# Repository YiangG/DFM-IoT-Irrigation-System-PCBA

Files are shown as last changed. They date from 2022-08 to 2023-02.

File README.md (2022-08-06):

# DFM-IoT-Irrigation-System-PCBA

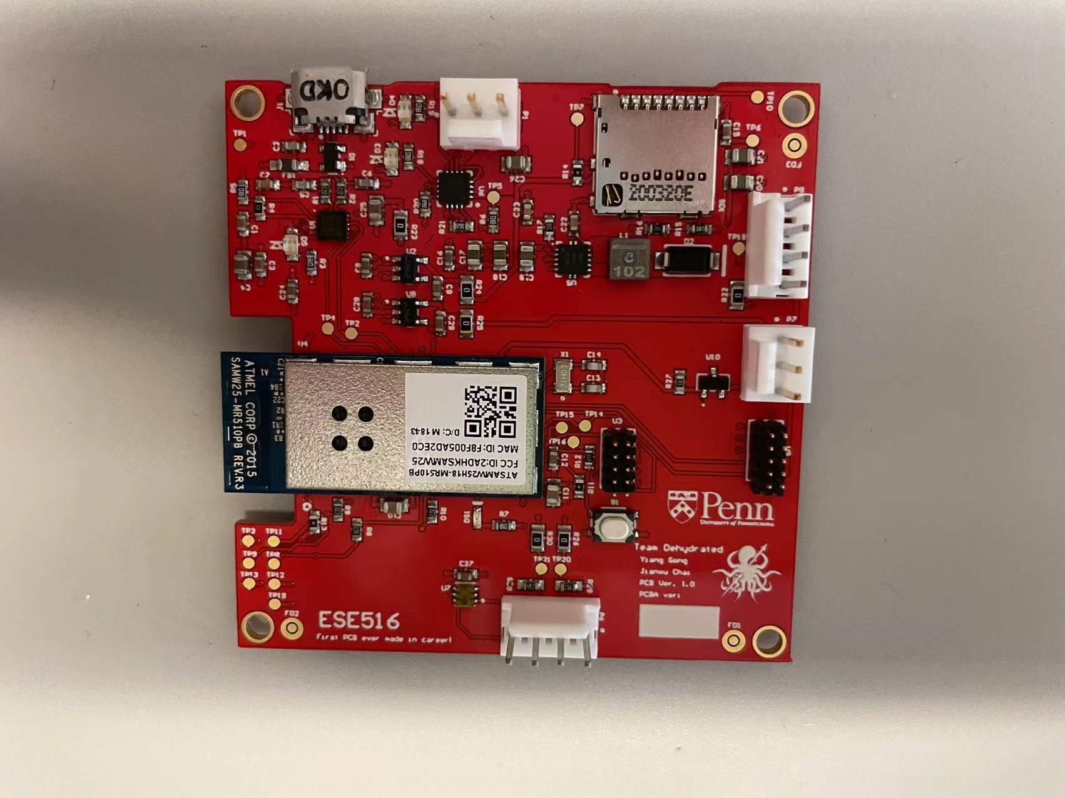
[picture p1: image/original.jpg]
original


This is the output file from Altium Designer from ESE516 class
## What it does
We decided to make a smart irrigation system which could measure the moisture level of soil and irrigate it when it is too dry.

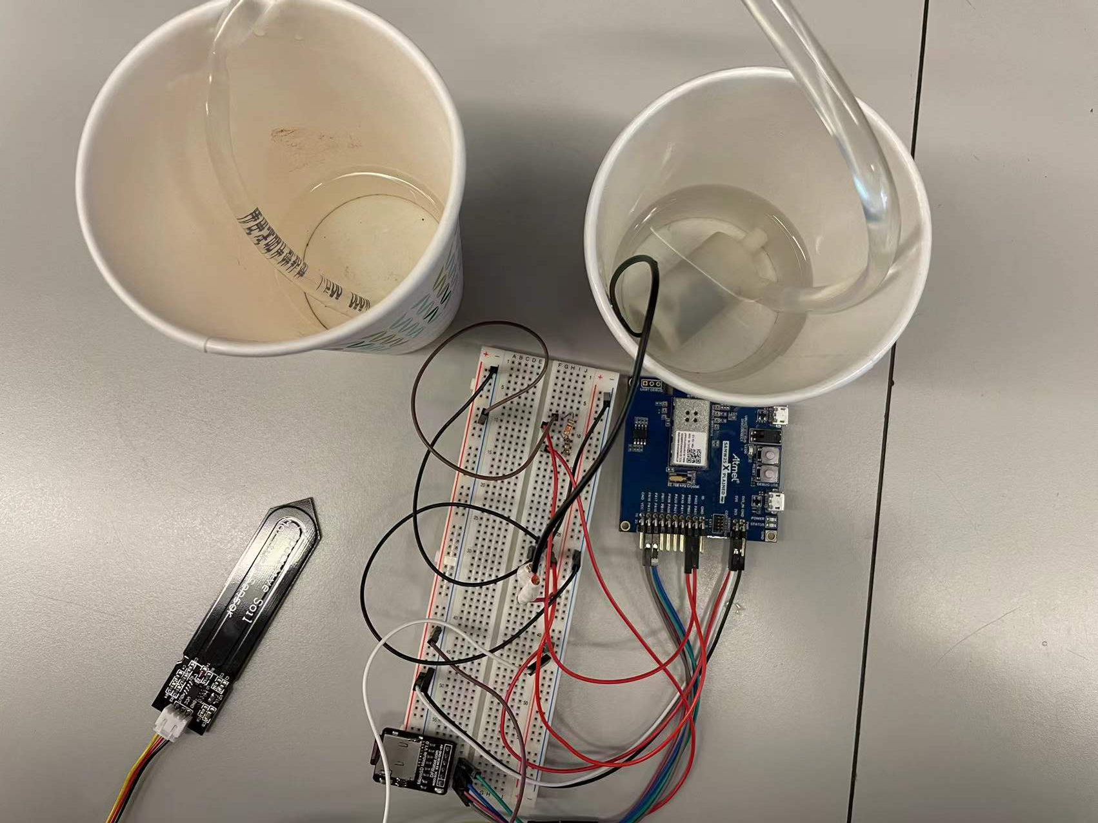
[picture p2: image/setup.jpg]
setup

https://www.youtube.com/watch?v=NsQ1t5cRwfQ

## Inspiration
This device is designed for people who love gardening but travel a lot. Once the device is installed, while the user is away from home, it could alert the user when the soil moisture level drops below a certain threshold, and the user could remotely control the device to water the plants, or to let the device decide when to irrigate the plants.

## How we built it
In this project, we followed the top-down design scheme. So, in the first place, we designed the overall functionalities of the system as shown in the system block diagram. The system is based on the SAMW25 MCU, and it communicate with the soil moisture sensor and the ambient light sensor via I2C and drive the pump and LED array with GPIO. Also, the MCU has the WINC1500 WIFI module so we used this feature to build an IoT product.

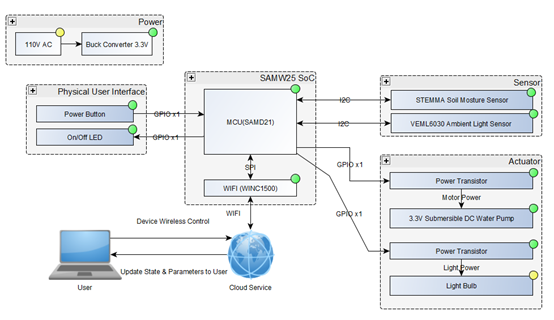
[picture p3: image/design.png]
design


Then we captured the schematics, and started PCBA layout in Altium Designer. The schematic and PCB layout are on the image files above. In the schematics, we used the hierarchical subsheet structure to simplify the main schematic and make it easy to read.

Then we selected proper components and layout them onto the PCBA file. We implemented our design in a 4 layers PCB. It’s quite an interesting experience of designing the PCB, and after that we send this PCB design to PCBWAY, a manufacture in Shenzhen China, to print it out.

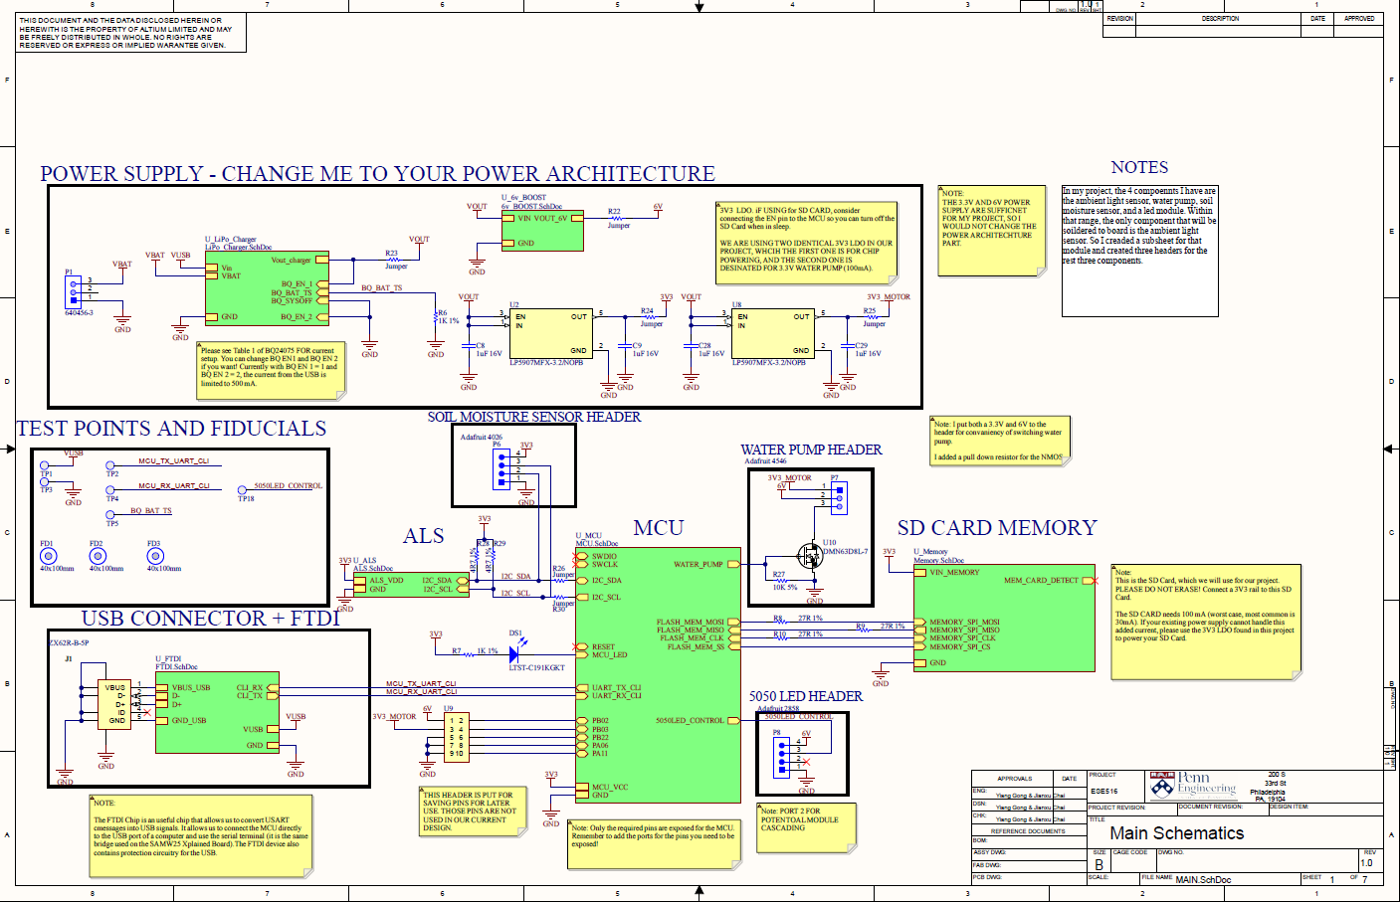
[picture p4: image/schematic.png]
schematic


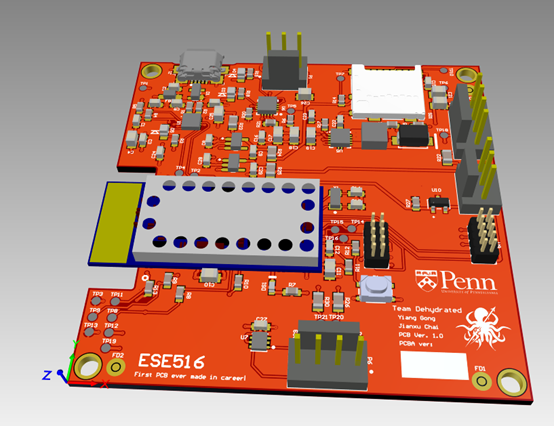
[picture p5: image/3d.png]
3d


After the hardware design, we started on the software side, which we implemented a bootloader, and utilized the FreeRTOS system on our project. Also, our board has command line interface, which we can type some instructions to the terminal and readout the sensor values (soil moisture sensor, IMU, ultrasonic sensor, etc.). Since it’s an IoT project, we implemented web interface (via NodeRed and IBM cloud) as well. The upstream data are being transmitted to the MQTT broker server first and then to the NodeRed interface, which is powered by IBM cloud. We can read sensor value and history in the web interface, as shown in picture above.

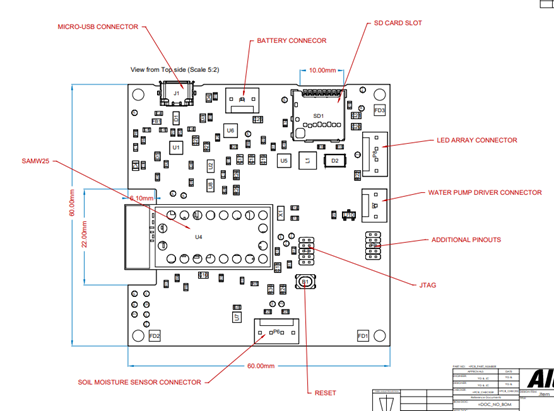
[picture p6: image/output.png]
output


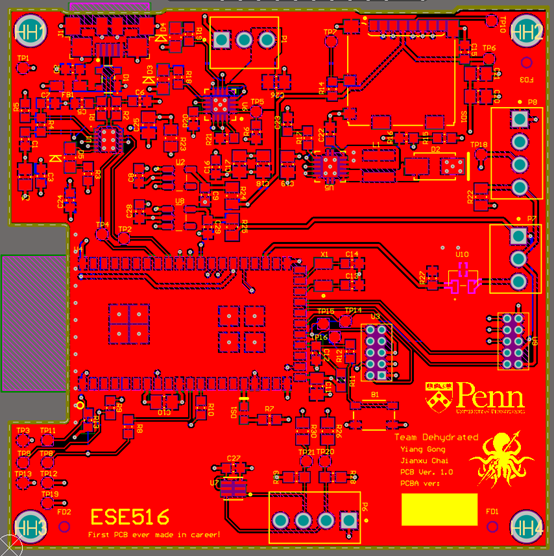
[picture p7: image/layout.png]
layout


## Challenges we ran into
The first challenge we met is the shortage of the parts we need. When it comes to select our parts, we have to update our BOM frequently, because some parts may be out of stock after a day. The second challenge we encountered is the design of our PCB board. Since it’s our first time to design the PCB board, it’s really hard for us to make the components clear and neat at the beginning. Fortunately, we finally improve the layout of our board to be clear and neat with the professor’s advice.

In addition, due to the Covid-19, the manufacture could not deliver our PCB board on time. Thus, we have to use SAMD21 board and don’t have time to debug our own board. Moreover, we struck into using ADC library with our soil moisture sensor. At the beginning, we couldn’t print a correct value of the output of our sensor. Also, we faced a challenge about sending message to MQTT and showing the value of the soil moisture sensor in a chart in Node Red.

## Accomplishments we are proud of
-A cool PCB board. -A system which can automatically water flowers according to the humidity. -Successfully implement ADC library and make the MCU constantly read the output of the soil moisture sensor. -Build an UI dashboard in Node Red -Apply FreeRTOS to do multi-thread tasks.

## What we learned:
-Basic knowledge about PCB board and its layout and design our own PCB board using Altium Designer. -Make the system do multi-tasks simultaneously -Design a PCB board using Altium Designer -Apply Mutex and Semaphore of FreeRTOS -Implement ADC library on SAMW 25 -Send sensor’s data to cloud using MQTT and Node Red

## What’s next:
We plan to add an ambient light sensor and test the whole project on our new board

## Limitation
In this project, we did not complete all the designated functionalities we plan to have, which namely, we have trouble interfacing with the ambient light sensor. After several days and nights of fighting the sensor driver, we decided to gave up on it and only have the soil moisture sensor and water pump functionalities. Also, due to the global pandemic, our boards shipment has been delayed by 2 weeks, so we did not get it on time for this project, so we implemented our project on the SAMW25 Xplained Pro development board instead.

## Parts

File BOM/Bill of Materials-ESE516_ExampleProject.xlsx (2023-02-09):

Line # | Name | Quantity | Description | Designator | Manufacturer 1 | Manufacturer Part Number 1 | Manufacturer Lifecycle 1 | Supplier 1 | Supplier Part Number 1 | Supplier Unit Price 1 | Supplier Subtotal 1
1 | PTS810 SJK 250 SMTR LFS | 1 | SWITCH TACTILE SPST-NO 0.05A 16V Tactile Switch SPST-NO Top Actuated Surface Mount | B1 | ITT C&K | PTS810SJK250SMTRLFS | Volume Production | NetroFlash | PTS810SJK250SMTRLFS | 0.29116 | 0.29116
2 | CAP 100nF 16V 0603(1608) | 5 | CAP 100nF 16V ±10% 0603 (1608 Metric) Thickness 1mm SMD | C1, C3, C7, C15, C22 | KEMET | C0603C104J4RACTU | Volume Production | ElectroShield | C0603C104J4RACTU | 0.0052 | 0.026
3 | CAP 10nF 16V 0603(1608) | 1 | CAP 10nF 16V ±10% 0603 (1608 Metric) Thickness 1mm SMD | C2 | Yageo | CC0603KRX7R7BB103 | Volume Production | Newark | 50AJ2712 | 0.012 | 0.012
4 | CAP 4.7uF 16V 0805(2012) | 3 | CAP 4.7uF 16V -20% to +80% 0805 (2012 Metric) Thickness 1.45mm SMD | C4, C25, C26 | Yageo | CC0805ZKY5V7BB475 | Volume Production | Newark | 69AH7357 | 0.038 | 0.114
5 | CAP 47pF 16V 0603(1608) | 2 | CAP 47pF 16V ±0.5pF 0603 (1608 Metric) Thickness 1mm SMD | C5, C6 | Kyocera AVX | 0603YA470KAT2A | Volume Production | Digi-Key | 478-11840-1-ND | 0.2 | 0.4
6 | CAP 1uF 16V 0603(1608) | 8 | CAP 1uF 16V ±5% 0603 (1608 Metric) Thickness 1mm SMD | C8, C9, C12, C16, C24, C27, C28, C29 | Yageo | CC0603KPX7R8BB105 | Volume Production | Digi-Key | 13-CC0603KPX7R8BB105CT-ND | 0.162 | 1.62
7 | CAP 10uF 16V 0805(2012) | 2 | CAP 10uF 16V ±10% 0805 (2012 Metric) Thickness 1.45mm SMD | C10, C11 | Yageo | CC0805MKX7R7BB106 | Volume Production | Eastek | CC0805MKX7R7BB106_D | 0.1295 | 0.259
8 | CAP 18pF 16V 0603(1608) | 2 | CAP 18pF 16V ±5% 0603 (1608 Metric) Thickness 1mm SMD | C13, C14 | KEMET | C0603C180J4GACTU | Volume Production | Newark | 96Y6992 | 0.03 | 0.06
9 | CAP 22uF 10V 0805(2012) | 5 | CAP 22uF 10V ±20% 0805 (2012 Metric) Thickness 1.45mm SMD | C17, C18, C19, C20, C21 | Yageo | CC0805MKX7R7BB106 | Volume Production | Mouser | 603-CC0805MKX77BB106 | 0.61 | 3.05
10 | CAP 820pF 10V 0603(1608) | 1 | CAP 820pF 10V ±10% 0603 (1608 Metric) Thickness 1mm SMD | C23 | Walsin Technologies | 0603B821K500CT | Volume Production | Quest | 0603B821K500CT | 0.021 | 0.021
11 | PRTR5V0U2X,215 | 1 | Ultra Low Capacitance Double Rail-to-Rail ESD Protection Diode, 5.5 V, 1 pF, -40 to 85 degC, 4-Pin SOT143B, RoHS, Tape and Reel | D1 | Nexperia | PRTR5V0U2X,215 | Volume Production | Anansix Microsemi | PRTR5V0U2X,215 | 0.137 | 0.137
12 | B340A-13-F | 1 | Surface Mount Schottky Barrier Rectifier, 40 V, 3 A, -55 to 150 degC, 2-Pin SMA, RoHS, Tape and Reel | D2 | Vishay Semiconductors | SSA34HE3_A/I | Volume Production | LTL Group | 4505426 | 0.139 | 0.139
13 | LTST-C170CKT | 2 | LED Uni-Color Red, 100 mW, 200 mA, -55 to 85 degC, 2-Pin SMD, RoHS, Tape and Reel | D3, D5 | Vishay Lite-On | LTST-C170AKT | Volume Production | Arrow Electronics | LTST-C170AKT | 0.3007 | 0.6014
14 | LTST-C170GKT | 1 | LED Uni-Color Green, 100 mW, 120 mA, -55 to 85 degC, 2-Pin SMD, RoHS, Tape and Reel | D4 | Vishay Lite-On | LTST-C170AKT | Volume Production | Arrow Electronics | LTST-C170AKT | 0.3007 | 0.3007
15 | LTST-C191KGKT | 1 | Chip LED, Green, 574 nm, 40 pF, -55 to 85 degC, 2-Pin SMD, RoHS, Tape and Reel | DS1 | Vishay Lite-On | LTST-C191GKT | Volume Production | Utmel Electronic | 456-LTST-C191GKT | 0.04596 | 0.04596
16 | BLM21PG221SN1D | 1 | Chip Ferrite Bead for Power Lines, 220 Ohm, 2000 mA, -55 to 125 degC, 2 x 1.25 x 1.05 mm SMD, Tape and Reel | FB1 | Bourns | MH2029-221Y | Volume Production | Utmel Electronic | 103-MH2029-221Y | 0.06204 | 0.06204
17 | 40x100mm | 3 | Fiducial 40x100mm | FD1, FD2, FD3
18 | ZX62R-B-5P | 1 | Connector; USBMicro-B,Reverse type, SMT; 5 Position; Right Angle | J1 | Hirose | ZX62R-B-5P(30) | Volume Production | Digi-Key | H125274CT-ND | 1.02 | 1.02
19 | XFL4020-102MEC | 1 | Shielded Power Inductor, 1 uH, 64 MHz, -40 to 125 degC, 2-Pin SMD, RoHS, Tape and Reel | L1 | Coilcraft | XFL4020-102MEC | Volume Production | NetroFlash | XFL4020-102MEC | 0.10197 | 0.10197
20 | 640456-3 | 2 | Male Header, Pitch 2.54 mm, 1 x 3 Position, Height 10.03 mm, Tail Length 3.56 mm, -55 to 105 degC | P1, P7 | Molex | 22-11-2032 | Volume Production | Freelance Electronics | 22-11-2032 | 0.13243 | 0.26486
21 | 640456-4 | 2 | Male Header, Pitch 2.54 mm, 1 x 4 Position, Height 10.03 mm, Tail Length 3.56 mm, RoHS, Bulk | P6, P8 | Molex | 22-11-2042 | Volume Production | Freelance Electronics | 22-11-2042 | 0.18322 | 0.36644
22 | 27R 1% 0603(1608) | 5 | 27R 0.1W 1% 0603 (1608 Metric) SMD | R1, R2, R8, R9, R10 | Yageo | RC0603FR-0727RL | Unknown | Digi-Key | 311-27.0HRCT-ND | 0.019 | 0.19
23 | 1K 1% 0603(1608) | 6 | 1K 0.1W 1% 0603 (1608 Metric) SMD | R3, R5, R6, R7, R18, R19 | Stackpole Electronics | RMCF0805FT1K00 | Volume Production | NAC Semi | RMCF0805FT1K00 | 0.006 | 0.036
24 | Jumper 0603(1608) | 1 | Jumper 0603 (1608 Metric) | R4 | Yageo | RC0603JR-130RL | Volume Production | Eastek | RC0603JR-130RL_D | 0.001 | 0.001
25 | 10K 1% 0603(1608) | 3 | 10K 0.1W 1% 0603 (1608 Metric) SMD | R11, R13, R14 | Stackpole Electronics | RMCF0603FT10K0 | Volume Production | Utmel Electronic | 762-RMCF0603FT10K0 | 0.00339 | 0.01017
26 | 100R 1% 0603(1608) | 1 | 100R 0.1W 1% 0603 (1608 Metric) SMD | R12 | Stackpole Electronics | RMCF0603FT100R | Volume Production | NetroFlash | RMCF0603FT100R | 0.00412 | 0.00412
27 | 150K 1% 0603(1608) | 1 | 150K 0.1W 1% 0603 (1608 Metric) SMD | R15 | Stackpole Electronics | RMCF0603FT150K | Volume Production | Utmel Electronic | 762-RMCF0603FT150K | 0.01128 | 0.01128
28 | 39K 1% 0603(1608) | 1 | 39K 0.1W 1% 0603 (1608 Metric) SMD | R16 | Vishay | CRCW060339K0FKEA | Volume Production | Newark | 42K3886 | 0.005 | 0.005
29 | 68K1 1% 0603(1608) | 1 | 68K1 0.1W 1% 0603 (1608 Metric) SMD | R17 | Bourns | CR0603-FX-6812ELF | Volume Production | Arrow Electronics | CR0603-FX-6812ELF | 0.0625 | 0.0625
30 | 1K13 1% 0603(1608) | 2 | 1K13 0.1W 1% 0603 (1608 Metric) SMD | R20, R21 | Panasonic | ERJ-3EKF1131V | Volume Production | Newark | 65T8317 | 0.002 | 0.004
31 | Jumper 0805(2012) | 6 | Jumper 0805 (2012 Metric) | R22, R23, R24, R25, R26, R30 | Yageo | AC0805JR-070RL | Volume Production | Eastek | AC0805JR-070RL_D | 0.00219 | 0.01314
32 | 10K 5% 0603(1608) | 1 | 10K 0.1W 5% 0603 (1608 Metric) SMD | R27 | Stackpole Electronics | RMCF0603FT10K0 | Volume Production | Utmel Electronic | 762-RMCF0603FT10K0 | 0.00339 | 0.00339
33 | 4R7 1% 0603(1608) | 2 | 4R7 0.1W 1% 0603 (1608 Metric) SMD | R28, R29 | Stackpole Electronics | RMCF0603FT4R70 | Volume Production | Arrow Electronics | RMCF0603FT4R70 | 0.0653 | 0.1306
34 | 104031-0811 | 1 | Micro SD Card, RA, -25 to 85 degC, 8-Pin SMD, RoHS, Tape and Reel | SD1 | Molex | 1040310811 | Unknown | LCSC | C585350 | 0.5871 | 0.5871
35 | 0.1" Pad | 20 | 0.1" Pad | TP1, TP2, TP3, TP4, TP5, TP6, TP7, TP8, TP9, TP10, TP11, TP12, TP13, TP14, TP15, TP16, TP18, TP19, TP20, TP21
36 | FT234XD-R | 1 | FT234XD USB to BASIC UART IC, -40 to +85 degC, 12-Pin DFN, Pb-Free, Tape and Reel | U1 | FTDI | FT234XD-R | Volume Production | Digi-Key | 768-1178-1-ND | 2.26 | 2.26
37 | LP5907MFX-3.2/NOPB | 2 | 250-mA, low-noise, high-PSRR, low-IQ, ultra-low-dropout voltage regulator with low-IQ & enable 5-SOT-23 -40 to 125 | U2, U8 | Texas Instruments | LP5907MFX-3.2/NOPB | Volume Production | ICSOSO Electronics Company Limited | LP5907MFX-3.2/NOPB | 0.298 | 0.596
38 | 20021111-00010T4LF | 1 | CONN HEADER 10POS UNSHD VERT T/H | U3 | Amphenol ICC / FCI | 20021111-00010T4LF | Unknown | Mouser | 649-221111-00010T4LF | 0.79 | 0.79
39 | SAMW25H18-MR510PB | 1 | RF TXRX MODULE WIFI TRACE ANT | U4 |  |  |  | Digikey | ATSAMW25H18-MR510PB-ND
40 | TPS61087DRCR | 1 | Boost Voltage Converter with 2.5 to 6 V Input and 3 to 18.5 V Output, -40 to 85 degC, 10-Pin SON (DRC), Green (RoHS & no Sb/Br) | U5 | Texas Instruments | TPS61080DRCR | Volume Production | ZTZ Technology Limited | TPS61080DRCR | 1.09 | 1.09
41 | BQ24075RGTRG4 | 1 | USB-Friendly Li-Ion Battery Charger and Power-Path Management IC, Vout 5.5 V, 4.3 V, -40 to 85 degC, 16-pin QFN (RGT), Green (RoHS & no Sb/Br) | U6 | Texas Instruments | BQ24079TRGTT | Volume Production | LKR | 719249 | 1.98 | 1.98
42 | TSL25911FN | 1 | Light-to-Digital Converter with I2C Interface, 2.7 to 3.6 V, -30 to 70 degC, FN-6, Pb-Free, Reel | U7 | ams TAOS | TSL25911FN | Volume Production | Utmel Electronic | 33-TSL25911FN | 3.15 | 3.15
43 |  | 1 | CONN HEADER 10POS UNSHD VERT T/H | U9 | Amphenol ICC / FCI | 20021111-00014T4LF | Unknown | Mouser | 649-221111-00014T4LF | 1.11 | 1.11
44 | DMN63D8L-7 | 1 | MOSFET N-CH 30V 350MA SOT23 | U10 | Diodes | DMN63D8L-7 | Volume Production | Utmel Electronic | 233-DMN63D8L-7 | 0.04259 | 0.04259
45 | ABS07-32.768KHz-T | 1 | Crystal, 32.768 kHz, 12.5 pF, -40 to 85 degC, SMD Low Profile 3.2 x 1.5 x 0.9 mm, Tape and Reel | X1 | Abracon | ABS07-32.768KHZ-9-H-T | Volume Production | Digi-Key | 535-15023-1-ND | 1.25 | 1.25

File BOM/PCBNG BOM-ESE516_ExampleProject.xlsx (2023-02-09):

Line # | Name | Description | Designator | Manufacturer 1 | Manufacturer Part Number 1 | Manufacturer Lifecycle 1 | Supplier 1 | Supplier Part Number 1 | Supplier Unit Price 1 | Supplier Subtotal 1
1 | PTS810 SJK 250 SMTR LFS | SWITCH TACTILE SPST-NO 0.05A 16V Tactile Switch SPST-NO Top Actuated Surface Mount | B1 | ITT C&K | PTS810SJK250SMTRLFS | Volume Production | NetroFlash | PTS810SJK250SMTRLFS | 0.29116 | 0.29116
2 | CAP 100nF 16V 0603(1608) | CAP 100nF 16V ±10% 0603 (1608 Metric) Thickness 1mm SMD | C1 | KEMET | C0603C104J4RACTU | Volume Production | ElectroShield | C0603C104J4RACTU | 0.0052 | 0.026
3 | CAP 10nF 16V 0603(1608) | CAP 10nF 16V ±10% 0603 (1608 Metric) Thickness 1mm SMD | C2 | Yageo | CC0603KRX7R7BB103 | Volume Production | Newark | 50AJ2712 | 0.012 | 0.012
2 | CAP 100nF 16V 0603(1608) | CAP 100nF 16V ±10% 0603 (1608 Metric) Thickness 1mm SMD | C3 | KEMET | C0603C104J4RACTU | Volume Production | ElectroShield | C0603C104J4RACTU | 0.0052 | 0.026
4 | CAP 4.7uF 16V 0805(2012) | CAP 4.7uF 16V -20% to +80% 0805 (2012 Metric) Thickness 1.45mm SMD | C4 | Yageo | CC0805ZKY5V7BB475 | Volume Production | Newark | 69AH7357 | 0.038 | 0.114
5 | CAP 47pF 16V 0603(1608) | CAP 47pF 16V ±0.5pF 0603 (1608 Metric) Thickness 1mm SMD | C5 | Kyocera AVX | 0603YA470KAT2A | Volume Production | Digi-Key | 478-11840-1-ND | 0.2 | 0.4
5 | CAP 47pF 16V 0603(1608) | CAP 47pF 16V ±0.5pF 0603 (1608 Metric) Thickness 1mm SMD | C6 | Kyocera AVX | 0603YA470KAT2A | Volume Production | Digi-Key | 478-11840-1-ND | 0.2 | 0.4
2 | CAP 100nF 16V 0603(1608) | CAP 100nF 16V ±10% 0603 (1608 Metric) Thickness 1mm SMD | C7 | KEMET | C0603C104J4RACTU | Volume Production | ElectroShield | C0603C104J4RACTU | 0.0052 | 0.026
6 | CAP 1uF 16V 0603(1608) | CAP 1uF 16V ±5% 0603 (1608 Metric) Thickness 1mm SMD | C8 | Yageo | CC0603KPX7R8BB105 | Volume Production | Digi-Key | 13-CC0603KPX7R8BB105CT-ND | 0.162 | 1.62
6 | CAP 1uF 16V 0603(1608) | CAP 1uF 16V ±5% 0603 (1608 Metric) Thickness 1mm SMD | C9 | Yageo | CC0603KPX7R8BB105 | Volume Production | Digi-Key | 13-CC0603KPX7R8BB105CT-ND | 0.162 | 1.62
7 | CAP 10uF 16V 0805(2012) | CAP 10uF 16V ±10% 0805 (2012 Metric) Thickness 1.45mm SMD | C10 | Yageo | CC0805MKX7R7BB106 | Volume Production | Eastek | CC0805MKX7R7BB106_D | 0.1295 | 0.259
7 | CAP 10uF 16V 0805(2012) | CAP 10uF 16V ±10% 0805 (2012 Metric) Thickness 1.45mm SMD | C11 | Yageo | CC0805MKX7R7BB106 | Volume Production | Eastek | CC0805MKX7R7BB106_D | 0.1295 | 0.259
6 | CAP 1uF 16V 0603(1608) | CAP 1uF 16V ±5% 0603 (1608 Metric) Thickness 1mm SMD | C12 | Yageo | CC0603KPX7R8BB105 | Volume Production | Digi-Key | 13-CC0603KPX7R8BB105CT-ND | 0.162 | 1.62
8 | CAP 18pF 16V 0603(1608) | CAP 18pF 16V ±5% 0603 (1608 Metric) Thickness 1mm SMD | C13 | KEMET | C0603C180J4GACTU | Volume Production | Newark | 96Y6992 | 0.03 | 0.06
8 | CAP 18pF 16V 0603(1608) | CAP 18pF 16V ±5% 0603 (1608 Metric) Thickness 1mm SMD | C14 | KEMET | C0603C180J4GACTU | Volume Production | Newark | 96Y6992 | 0.03 | 0.06
2 | CAP 100nF 16V 0603(1608) | CAP 100nF 16V ±10% 0603 (1608 Metric) Thickness 1mm SMD | C15 | KEMET | C0603C104J4RACTU | Volume Production | ElectroShield | C0603C104J4RACTU | 0.0052 | 0.026
6 | CAP 1uF 16V 0603(1608) | CAP 1uF 16V ±5% 0603 (1608 Metric) Thickness 1mm SMD | C16 | Yageo | CC0603KPX7R8BB105 | Volume Production | Digi-Key | 13-CC0603KPX7R8BB105CT-ND | 0.162 | 1.62
9 | CAP 22uF 10V 0805(2012) | CAP 22uF 10V ±20% 0805 (2012 Metric) Thickness 1.45mm SMD | C17 | Yageo | CC0805MKX7R7BB106 | Volume Production | Mouser | 603-CC0805MKX77BB106 | 0.61 | 3.05
9 | CAP 22uF 10V 0805(2012) | CAP 22uF 10V ±20% 0805 (2012 Metric) Thickness 1.45mm SMD | C18 | Yageo | CC0805MKX7R7BB106 | Volume Production | Mouser | 603-CC0805MKX77BB106 | 0.61 | 3.05
9 | CAP 22uF 10V 0805(2012) | CAP 22uF 10V ±20% 0805 (2012 Metric) Thickness 1.45mm SMD | C19 | Yageo | CC0805MKX7R7BB106 | Volume Production | Mouser | 603-CC0805MKX77BB106 | 0.61 | 3.05
9 | CAP 22uF 10V 0805(2012) | CAP 22uF 10V ±20% 0805 (2012 Metric) Thickness 1.45mm SMD | C20 | Yageo | CC0805MKX7R7BB106 | Volume Production | Mouser | 603-CC0805MKX77BB106 | 0.61 | 3.05
9 | CAP 22uF 10V 0805(2012) | CAP 22uF 10V ±20% 0805 (2012 Metric) Thickness 1.45mm SMD | C21 | Yageo | CC0805MKX7R7BB106 | Volume Production | Mouser | 603-CC0805MKX77BB106 | 0.61 | 3.05
2 | CAP 100nF 16V 0603(1608) | CAP 100nF 16V ±10% 0603 (1608 Metric) Thickness 1mm SMD | C22 | KEMET | C0603C104J4RACTU | Volume Production | ElectroShield | C0603C104J4RACTU | 0.0052 | 0.026
10 | CAP 820pF 10V 0603(1608) | CAP 820pF 10V ±10% 0603 (1608 Metric) Thickness 1mm SMD | C23 | Walsin Technologies | 0603B821K500CT | Volume Production | Quest | 0603B821K500CT | 0.021 | 0.021
6 | CAP 1uF 16V 0603(1608) | CAP 1uF 16V ±5% 0603 (1608 Metric) Thickness 1mm SMD | C24 | Yageo | CC0603KPX7R8BB105 | Volume Production | Digi-Key | 13-CC0603KPX7R8BB105CT-ND | 0.162 | 1.62
4 | CAP 4.7uF 16V 0805(2012) | CAP 4.7uF 16V -20% to +80% 0805 (2012 Metric) Thickness 1.45mm SMD | C25 | Yageo | CC0805ZKY5V7BB475 | Volume Production | Newark | 69AH7357 | 0.038 | 0.114
4 | CAP 4.7uF 16V 0805(2012) | CAP 4.7uF 16V -20% to +80% 0805 (2012 Metric) Thickness 1.45mm SMD | C26 | Yageo | CC0805ZKY5V7BB475 | Volume Production | Newark | 69AH7357 | 0.038 | 0.114
6 | CAP 1uF 16V 0603(1608) | CAP 1uF 16V ±5% 0603 (1608 Metric) Thickness 1mm SMD | C27 | Yageo | CC0603KPX7R8BB105 | Volume Production | Digi-Key | 13-CC0603KPX7R8BB105CT-ND | 0.162 | 1.62
6 | CAP 1uF 16V 0603(1608) | CAP 1uF 16V ±5% 0603 (1608 Metric) Thickness 1mm SMD | C28 | Yageo | CC0603KPX7R8BB105 | Volume Production | Digi-Key | 13-CC0603KPX7R8BB105CT-ND | 0.162 | 1.62
6 | CAP 1uF 16V 0603(1608) | CAP 1uF 16V ±5% 0603 (1608 Metric) Thickness 1mm SMD | C29 | Yageo | CC0603KPX7R8BB105 | Volume Production | Digi-Key | 13-CC0603KPX7R8BB105CT-ND | 0.162 | 1.62
11 | PRTR5V0U2X,215 | Ultra Low Capacitance Double Rail-to-Rail ESD Protection Diode, 5.5 V, 1 pF, -40 to 85 degC, 4-Pin SOT143B, RoHS, Tape and Reel | D1 | Nexperia | PRTR5V0U2X,215 | Volume Production | Anansix Microsemi | PRTR5V0U2X,215 | 0.137 | 0.137
12 | B340A-13-F | Surface Mount Schottky Barrier Rectifier, 40 V, 3 A, -55 to 150 degC, 2-Pin SMA, RoHS, Tape and Reel | D2 | Vishay Semiconductors | SSA34HE3_A/I | Volume Production | LTL Group | 4505426 | 0.139 | 0.139
13 | LTST-C170CKT | LED Uni-Color Red, 100 mW, 200 mA, -55 to 85 degC, 2-Pin SMD, RoHS, Tape and Reel | D3 | Vishay Lite-On | LTST-C170AKT | Volume Production | Arrow Electronics | LTST-C170AKT | 0.3007 | 0.6014
14 | LTST-C170GKT | LED Uni-Color Green, 100 mW, 120 mA, -55 to 85 degC, 2-Pin SMD, RoHS, Tape and Reel | D4 | Vishay Lite-On | LTST-C170AKT | Volume Production | Arrow Electronics | LTST-C170AKT | 0.3007 | 0.3007
13 | LTST-C170CKT | LED Uni-Color Red, 100 mW, 200 mA, -55 to 85 degC, 2-Pin SMD, RoHS, Tape and Reel | D5 | Vishay Lite-On | LTST-C170AKT | Volume Production | Arrow Electronics | LTST-C170AKT | 0.3007 | 0.6014
15 | LTST-C191KGKT | Chip LED, Green, 574 nm, 40 pF, -55 to 85 degC, 2-Pin SMD, RoHS, Tape and Reel | DS1 | Vishay Lite-On | LTST-C191GKT | Volume Production | Utmel Electronic | 456-LTST-C191GKT | 0.04596 | 0.04596
16 | BLM21PG221SN1D | Chip Ferrite Bead for Power Lines, 220 Ohm, 2000 mA, -55 to 125 degC, 2 x 1.25 x 1.05 mm SMD, Tape and Reel | FB1 | Bourns | MH2029-221Y | Volume Production | Utmel Electronic | 103-MH2029-221Y | 0.06204 | 0.06204
17 | 40x100mm | Fiducial 40x100mm | FD1
17 | 40x100mm | Fiducial 40x100mm | FD2
17 | 40x100mm | Fiducial 40x100mm | FD3
18 | ZX62R-B-5P | Connector; USBMicro-B,Reverse type, SMT; 5 Position; Right Angle | J1 | Hirose | ZX62R-B-5P(30) | Volume Production | Digi-Key | H125274CT-ND | 1.02 | 1.02
19 | XFL4020-102MEC | Shielded Power Inductor, 1 uH, 64 MHz, -40 to 125 degC, 2-Pin SMD, RoHS, Tape and Reel | L1 | Coilcraft | XFL4020-102MEC | Volume Production | NetroFlash | XFL4020-102MEC | 0.10197 | 0.10197
20 | 640456-3 | Male Header, Pitch 2.54 mm, 1 x 3 Position, Height 10.03 mm, Tail Length 3.56 mm, -55 to 105 degC | P1 | Molex | 22-11-2032 | Volume Production | Freelance Electronics | 22-11-2032 | 0.13243 | 0.26486
21 | 640456-4 | Male Header, Pitch 2.54 mm, 1 x 4 Position, Height 10.03 mm, Tail Length 3.56 mm, RoHS, Bulk | P6 | Molex | 22-11-2042 | Volume Production | Freelance Electronics | 22-11-2042 | 0.18322 | 0.36644
20 | 640456-3 | Male Header, Pitch 2.54 mm, 1 x 3 Position, Height 10.03 mm, Tail Length 3.56 mm, -55 to 105 degC | P7 | Molex | 22-11-2032 | Volume Production | Freelance Electronics | 22-11-2032 | 0.13243 | 0.26486
21 | 640456-4 | Male Header, Pitch 2.54 mm, 1 x 4 Position, Height 10.03 mm, Tail Length 3.56 mm, RoHS, Bulk | P8 | Molex | 22-11-2042 | Volume Production | Freelance Electronics | 22-11-2042 | 0.18322 | 0.36644
22 | 27R 1% 0603(1608) | 27R 0.1W 1% 0603 (1608 Metric) SMD | R1 | Yageo | RC0603FR-0727RL | Unknown | Digi-Key | 311-27.0HRCT-ND | 0.019 | 0.19
22 | 27R 1% 0603(1608) | 27R 0.1W 1% 0603 (1608 Metric) SMD | R2 | Yageo | RC0603FR-0727RL | Unknown | Digi-Key | 311-27.0HRCT-ND | 0.019 | 0.19
23 | 1K 1% 0603(1608) | 1K 0.1W 1% 0603 (1608 Metric) SMD | R3 | Stackpole Electronics | RMCF0805FT1K00 | Volume Production | NAC Semi | RMCF0805FT1K00 | 0.006 | 0.036
24 | Jumper 0603(1608) | Jumper 0603 (1608 Metric) | R4 | Yageo | RC0603JR-130RL | Volume Production | Eastek | RC0603JR-130RL_D | 0.001 | 0.001
23 | 1K 1% 0603(1608) | 1K 0.1W 1% 0603 (1608 Metric) SMD | R5 | Stackpole Electronics | RMCF0805FT1K00 | Volume Production | NAC Semi | RMCF0805FT1K00 | 0.006 | 0.036
23 | 1K 1% 0603(1608) | 1K 0.1W 1% 0603 (1608 Metric) SMD | R6 | Stackpole Electronics | RMCF0805FT1K00 | Volume Production | NAC Semi | RMCF0805FT1K00 | 0.006 | 0.036
23 | 1K 1% 0603(1608) | 1K 0.1W 1% 0603 (1608 Metric) SMD | R7 | Stackpole Electronics | RMCF0805FT1K00 | Volume Production | NAC Semi | RMCF0805FT1K00 | 0.006 | 0.036
22 | 27R 1% 0603(1608) | 27R 0.1W 1% 0603 (1608 Metric) SMD | R8 | Yageo | RC0603FR-0727RL | Unknown | Digi-Key | 311-27.0HRCT-ND | 0.019 | 0.19
22 | 27R 1% 0603(1608) | 27R 0.1W 1% 0603 (1608 Metric) SMD | R9 | Yageo | RC0603FR-0727RL | Unknown | Digi-Key | 311-27.0HRCT-ND | 0.019 | 0.19
22 | 27R 1% 0603(1608) | 27R 0.1W 1% 0603 (1608 Metric) SMD | R10 | Yageo | RC0603FR-0727RL | Unknown | Digi-Key | 311-27.0HRCT-ND | 0.019 | 0.19
25 | 10K 1% 0603(1608) | 10K 0.1W 1% 0603 (1608 Metric) SMD | R11 | Stackpole Electronics | RMCF0603FT10K0 | Volume Production | Utmel Electronic | 762-RMCF0603FT10K0 | 0.00339 | 0.01017
26 | 100R 1% 0603(1608) | 100R 0.1W 1% 0603 (1608 Metric) SMD | R12 | Stackpole Electronics | RMCF0603FT100R | Volume Production | NetroFlash | RMCF0603FT100R | 0.00412 | 0.00412
25 | 10K 1% 0603(1608) | 10K 0.1W 1% 0603 (1608 Metric) SMD | R13 | Stackpole Electronics | RMCF0603FT10K0 | Volume Production | Utmel Electronic | 762-RMCF0603FT10K0 | 0.00339 | 0.01017
25 | 10K 1% 0603(1608) | 10K 0.1W 1% 0603 (1608 Metric) SMD | R14 | Stackpole Electronics | RMCF0603FT10K0 | Volume Production | Utmel Electronic | 762-RMCF0603FT10K0 | 0.00339 | 0.01017
27 | 150K 1% 0603(1608) | 150K 0.1W 1% 0603 (1608 Metric) SMD | R15 | Stackpole Electronics | RMCF0603FT150K | Volume Production | Utmel Electronic | 762-RMCF0603FT150K | 0.01128 | 0.01128
28 | 39K 1% 0603(1608) | 39K 0.1W 1% 0603 (1608 Metric) SMD | R16 | Vishay | CRCW060339K0FKEA | Volume Production | Newark | 42K3886 | 0.005 | 0.005
29 | 68K1 1% 0603(1608) | 68K1 0.1W 1% 0603 (1608 Metric) SMD | R17 | Bourns | CR0603-FX-6812ELF | Volume Production | Arrow Electronics | CR0603-FX-6812ELF | 0.0625 | 0.0625
23 | 1K 1% 0603(1608) | 1K 0.1W 1% 0603 (1608 Metric) SMD | R18 | Stackpole Electronics | RMCF0805FT1K00 | Volume Production | NAC Semi | RMCF0805FT1K00 | 0.006 | 0.036
23 | 1K 1% 0603(1608) | 1K 0.1W 1% 0603 (1608 Metric) SMD | R19 | Stackpole Electronics | RMCF0805FT1K00 | Volume Production | NAC Semi | RMCF0805FT1K00 | 0.006 | 0.036
30 | 1K13 1% 0603(1608) | 1K13 0.1W 1% 0603 (1608 Metric) SMD | R20 | Panasonic | ERJ-3EKF1131V | Volume Production | Newark | 65T8317 | 0.002 | 0.004
30 | 1K13 1% 0603(1608) | 1K13 0.1W 1% 0603 (1608 Metric) SMD | R21 | Panasonic | ERJ-3EKF1131V | Volume Production | Newark | 65T8317 | 0.002 | 0.004
31 | Jumper 0805(2012) | Jumper 0805 (2012 Metric) | R22 | Yageo | AC0805JR-070RL | Volume Production | Eastek | AC0805JR-070RL_D | 0.00219 | 0.01314
31 | Jumper 0805(2012) | Jumper 0805 (2012 Metric) | R23 | Yageo | AC0805JR-070RL | Volume Production | Eastek | AC0805JR-070RL_D | 0.00219 | 0.01314
31 | Jumper 0805(2012) | Jumper 0805 (2012 Metric) | R24 | Yageo | AC0805JR-070RL | Volume Production | Eastek | AC0805JR-070RL_D | 0.00219 | 0.01314
31 | Jumper 0805(2012) | Jumper 0805 (2012 Metric) | R25 | Yageo | AC0805JR-070RL | Volume Production | Eastek | AC0805JR-070RL_D | 0.00219 | 0.01314
31 | Jumper 0805(2012) | Jumper 0805 (2012 Metric) | R26 | Yageo | AC0805JR-070RL | Volume Production | Eastek | AC0805JR-070RL_D | 0.00219 | 0.01314
32 | 10K 5% 0603(1608) | 10K 0.1W 5% 0603 (1608 Metric) SMD | R27 | Stackpole Electronics | RMCF0603FT10K0 | Volume Production | Utmel Electronic | 762-RMCF0603FT10K0 | 0.00339 | 0.00339
33 | 4R7 1% 0603(1608) | 4R7 0.1W 1% 0603 (1608 Metric) SMD | R28 | Stackpole Electronics | RMCF0603FT4R70 | Volume Production | Arrow Electronics | RMCF0603FT4R70 | 0.0653 | 0.1306
33 | 4R7 1% 0603(1608) | 4R7 0.1W 1% 0603 (1608 Metric) SMD | R29 | Stackpole Electronics | RMCF0603FT4R70 | Volume Production | Arrow Electronics | RMCF0603FT4R70 | 0.0653 | 0.1306
31 | Jumper 0805(2012) | Jumper 0805 (2012 Metric) | R30 | Yageo | AC0805JR-070RL | Volume Production | Eastek | AC0805JR-070RL_D | 0.00219 | 0.01314
34 | 104031-0811 | Micro SD Card, RA, -25 to 85 degC, 8-Pin SMD, RoHS, Tape and Reel | SD1 | Molex | 1040310811 | Unknown | LCSC | C585350 | 0.5871 | 0.5871
35 | 0.1" Pad | 0.1" Pad | TP1
35 | 0.1" Pad | 0.1" Pad | TP2
35 | 0.1" Pad | 0.1" Pad | TP3
35 | 0.1" Pad | 0.1" Pad | TP4
35 | 0.1" Pad | 0.1" Pad | TP5
35 | 0.1" Pad | 0.1" Pad | TP6
35 | 0.1" Pad | 0.1" Pad | TP7
35 | 0.1" Pad | 0.1" Pad | TP8
35 | 0.1" Pad | 0.1" Pad | TP9
35 | 0.1" Pad | 0.1" Pad | TP10
35 | 0.1" Pad | 0.1" Pad | TP11
35 | 0.1" Pad | 0.1" Pad | TP12
35 | 0.1" Pad | 0.1" Pad | TP13
35 | 0.1" Pad | 0.1" Pad | TP14
35 | 0.1" Pad | 0.1" Pad | TP15
35 | 0.1" Pad | 0.1" Pad | TP16
35 | 0.1" Pad | 0.1" Pad | TP18
35 | 0.1" Pad | 0.1" Pad | TP19
35 | 0.1" Pad | 0.1" Pad | TP20
35 | 0.1" Pad | 0.1" Pad | TP21
36 | FT234XD-R | FT234XD USB to BASIC UART IC, -40 to +85 degC, 12-Pin DFN, Pb-Free, Tape and Reel | U1 | FTDI | FT234XD-R | Volume Production | Digi-Key | 768-1178-1-ND | 2.26 | 2.26
37 | LP5907MFX-3.2/NOPB | 250-mA, low-noise, high-PSRR, low-IQ, ultra-low-dropout voltage regulator with low-IQ & enable 5-SOT-23 -40 to 125 | U2 | Texas Instruments | LP5907MFX-3.2/NOPB | Volume Production | ICSOSO Electronics Company Limited | LP5907MFX-3.2/NOPB | 0.298 | 0.596
38 | 20021111-00010T4LF | CONN HEADER 10POS UNSHD VERT T/H | U3 | Amphenol ICC / FCI | 20021111-00010T4LF | Unknown | Mouser | 649-221111-00010T4LF | 0.79 | 0.79
39 | SAMW25H18-MR510PB | RF TXRX MODULE WIFI TRACE ANT | U4 |  |  |  | Digikey | ATSAMW25H18-MR510PB-ND
40 | TPS61087DRCR | Boost Voltage Converter with 2.5 to 6 V Input and 3 to 18.5 V Output, -40 to 85 degC, 10-Pin SON (DRC), Green (RoHS & no Sb/Br) | U5 | Texas Instruments | TPS61080DRCR | Volume Production | ZTZ Technology Limited | TPS61080DRCR | 1.09 | 1.09
41 | BQ24075RGTRG4 | USB-Friendly Li-Ion Battery Charger and Power-Path Management IC, Vout 5.5 V, 4.3 V, -40 to 85 degC, 16-pin QFN (RGT), Green (RoHS & no Sb/Br) | U6 | Texas Instruments | BQ24079TRGTT | Volume Production | LKR | 719249 | 1.98 | 1.98
42 | TSL25911FN | Light-to-Digital Converter with I2C Interface, 2.7 to 3.6 V, -30 to 70 degC, FN-6, Pb-Free, Reel | U7 | ams TAOS | TSL25911FN | Volume Production | Utmel Electronic | 33-TSL25911FN | 3.15 | 3.15
37 | LP5907MFX-3.2/NOPB | 250-mA, low-noise, high-PSRR, low-IQ, ultra-low-dropout voltage regulator with low-IQ & enable 5-SOT-23 -40 to 125 | U8 | Texas Instruments | LP5907MFX-3.2/NOPB | Volume Production | ICSOSO Electronics Company Limited | LP5907MFX-3.2/NOPB | 0.298 | 0.596
43 |  | CONN HEADER 10POS UNSHD VERT T/H | U9 | Amphenol ICC / FCI | 20021111-00014T4LF | Unknown | Mouser | 649-221111-00014T4LF | 1.11 | 1.11
44 | DMN63D8L-7 | MOSFET N-CH 30V 350MA SOT23 | U10 | Diodes | DMN63D8L-7 | Volume Production | Utmel Electronic | 233-DMN63D8L-7 | 0.04259 | 0.04259
45 | ABS07-32.768KHz-T | Crystal, 32.768 kHz, 12.5 pF, -40 to 85 degC, SMD Low Profile 3.2 x 1.5 x 0.9 mm, Tape and Reel | X1 | Abracon | ABS07-32.768KHZ-9-H-T | Volume Production | Digi-Key | 535-15023-1-ND | 1.25 | 1.25
